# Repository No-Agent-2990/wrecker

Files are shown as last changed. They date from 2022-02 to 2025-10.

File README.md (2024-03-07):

# Wrecker
Mostly 3D printed design for linear drive machine. 3" of travel, compact and economical. 



(Safe) Video https://imgur.com/a/8FI21lm

Stainless Steel 1/4-20 rod is used though the load bearing assembly it is quite sturdy.

I apologize to all our metric friends for using imperial hardware, but it's cheap and easy to find here. I may do a version for M6 rod if there is some demand.

# Bill of Materials

## Filament
- PLA, PLA+, or PAL Pro

## Electronics:
- ESP32 Arduino - Hitlego PN ESP-WROOM-32 or eq
- 7x3cm proto PCB perfboard - from Elegoo CA-EL-CP-021 kit or eq
- 24VDC 4A power supply with barrel connector output - ALITOVE ALT-2404 or eq. An old 19.5V laptop supply should work too though a little slower.
- Barrel connector extension cord - must match 24VDC supply
- 24V to Micro USB 5V converter
- NEMA23 56mm Stepper, Bipolar, 2.8A, 2.5mH, 1.8deg - Steppers Online PN 23HS22-2804S or similar
- TB6600 Stepper motor driver
- (2) Hall Effect sensors AH3574-P-A
- 40mm Fan (24V or 5V) - 5V if powering from Arduino (recommended)
- (2) 10K linear potentiometers
- (2) 6" or longer servo extensions

## Hardware
- (1 or 2) 1/4-20 all-threaded Stainless Steel rod, 24" (304 or 18/8)
- 1/4-20 Hex coupler
- (6) 1/4-20 hex nuts
- (4) 1/4-20 washers
- (6) M4x25mm Cheese head
- (4) M4 rubber Grommets or (8) M4 rubber washers
- (4) M4 hex nuts
- (4) M4 lock washers
- (16) M3x8mm flat-head?
- (2) 1/4" dia,  1/16" thick disc magnets

## Other
- Attachment of your choice! End effector files compatible with vacuum-lock attachments and fleshlight are provided.

# Printing

- PLA is the recommended material. Its hard, smooth and abrasion resistant. It is not heat resistant!
- Print the STL files in the orientation provided.
- Files designed for printer line width of 0.5mm and later height of 0.25mm. This works well with 0.4mm nozzle
- 3 walls, 20% 3D infill like cubic

*No supports should be needed*

# Mechanical Assembly

## Preparation

## Stepper Driver setup
- Set current dip switch for 2.5A current limit
- Set dip switch for steps per pulse (micro-steps) to 32

### Base

Tap all the M3 holes in base for cover.
Tap M3 holes for TB6600 mounting.
Tap M3 hole for cable clamp
Press fit 1/4-20 nut into pocket, use 1/4 bolt from below to help seat if needed. If not secure, melt plastic around edge.
Tap the M4 holes for the handle.

### Cover

Attach plug to fan wires (if none), will need mate for attaching to proto board
Mount fan on inside and grill on outside using 4x M3x12mm flathead screws, lockwashers and nuts.
*Make sure airflow direction is _into_ case.*

### Slide

Remove and blobs and bumps with sharp knife. Clean out any crud in tube with 1/4" drill.
Put a drop of glue in the pockets, then push magnets into each pocket. Remove any excess glue.

### Pinion

Clean up gear teeth, shaft hole as needed.
Insert M2 hex nut into pocket in shaft, thread M2x4mm grub screw in nut, leave flush.

### Vacuum lock effector

Coat with a couple coats of spray-on acrylic to seal.

## Hall sensors

Cut servo extension leaving about 6 in" on the female end.
Attach wires to the 3 leads of female end, heat shrink. 
- Red: VDD pin
- Black: GND pin
- White: OUT pin

## Assembly

### Servo motor
*if using grommets*:
Place M4 grommets into base holes, and push M4x25mm throuh grommets from slide side to motor side

*if using rubber washers*:
Place M4x25mm through rubber washer, then through base, then add 2nd rubber washer.

Place motor over screw ends, with leads up. Add lock washer and nut to each screw, tighten.

### PCB
Mount 3x7 PCB with ESP32, wiring attached tp 4 mounting bosses with #2x1/4" self-tapping screws.

### 24V to USB converter

Mount to side of vertical fin with M3x8mm screws. Plug micro-usb end into ESP32.

### TB6600
Mount to base holes with M3x8mm cheese head screws.

Cut barrel extension cable near male end and discard male end and strip wire ends.
Twist + wire from barrel connector and + wire from 24V USB converter together and insert into (+) DC input

Twist - wire from barrel connector and - wire from 24V USB converter together and insert into (-) DC input
***OBSERVE POLARITY CAREFULLY***

See wiring section for details on connecting control signals to TB6600.

### Slide
Cut 8" piece of 1/4-20 rod, de-burr and reform threads with nut.
*(Note: If you don't care if the machine can be broken down for storage, you can just used a single 16~20" piece)*
Place through tube in slide. 
Add washer to end w/o the nut pocket.
Add nuts to both ends of the rod. Set nut on end with pocket flush with rod.
Tight nut on other end to draw nut into pocket. Torque firmly.

### Hall sensors
Slide hall sensors fully into troughs, angled face up.
Secure with dab of hot glue.

### Vacuum lock effector

Cut 12" length of 1/4-20 SS rod. Deburr rod ends, thread nut over to restore threads.
Place rod through tube. 
Thread hex not on tip end of rod until rod is flush with nut. 
Place washer on other end of rod, then nut. Tighten nut with whrench until top nut is pulled fully into pocket.

## Post-Assembly

Lubricate slide with silicone lubricant oil (not grease).
Lubricate pinion gear with silicone grease.

# Wiring

*add diagram here*

I recommned installing 0.1" center headers on the protoboard and connecting the control signals via jumpers or servo plugs.

The default ESP32 pins used are given in the arduino sketch ino file source code:
```
const int pulsePin = 23;          <- This is the stepper driver "step" pulse output pin
const int dirPin  = 22;           <- This is the stepper driver "direction" control output pin
const int enaPin = 21;            <- This is the stepper driver enable output pin
const int limitBackPin = 36;      <- This is the front hall sensor input pin
const int limitFwdPin = 39;       <- This is the rear hall sensor input pin
const int speedAdcPin = 34;       <- Speed potentionmeter analog input pin
const int strokeAdcPin = 35;      <- Length potentiometer analog input pin
```
Configure TB6600 control wiring for common ground by connection the "-" terminal of each input of the TB6600 to arduino ground. 
*Note that the TB6600 control input grounds and TB6600 power ground are all isolated from eachother inside the TB6600!* 

Connect the appropriate ("pulse", "dir", "ena") GPIO pin of the ESP32 to the appropriate (+) control inputs on the TB6600.

Arduino sketch will drive the pin high (3.3V) to activate.

Connect hall sensors to ESP32 3.3V power (red wire), gnd (black), and appropriate GPIO pins (white).
*Note that the EPS32 signals are 3.3V IO, and do not support 5V levels!*

# Arduino
Code provided is written for the ESP32 which has dual 240MHz cores, and can run the stepper at its highest rate easily. It also has Wifi functionality built in. Any Arduino or other controller could probably be used but will not work with the provided code.

I used this stepper lib:

https://github.com/gin66/FastAccelStepper

I used these tutorials to develop the wifi and webserver:

https://randomnerdtutorials.com/esp32-dual-core-arduino-ide/

https://randomnerdtutorials.com/esp32-servo-motor-web-server-arduino-ide/

The randomnerdtutorials.com site has good tuturial how to install the needed components in the IDE. It's a bit complicated.

## Build Setup

## Code

All the sketch code is in the main ino file.

The network.h file has wifi network setup.

## Configuration

# Operation

Attach rod segment with end effector to slide shaft rod using the hex coupler with a additional nut on each side. Tight the nuts to lock in place. A 3D printable finger wrench is included.

Plug in power, wait for Wifi to initialize and/or connect, and the linear drive to auto-home. 
Adjust speed/stroke with sliders as desired.

If no device is connected to the web server, the on-board control knobs remain active. Once a web client connects, they knobs are inactive. If the web client disconnects, the knobs become active again.
...

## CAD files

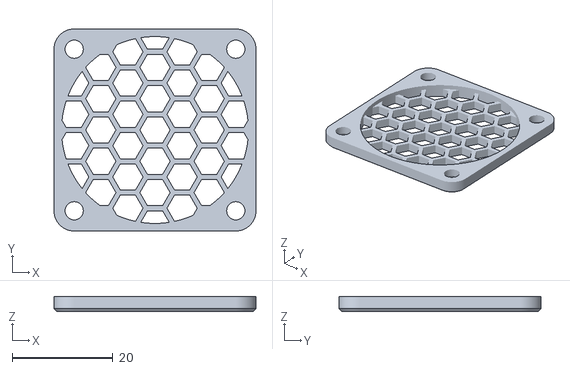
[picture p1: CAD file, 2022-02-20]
stl/fan-FanGrille.stl
40.0 x 40.0 x 3.00

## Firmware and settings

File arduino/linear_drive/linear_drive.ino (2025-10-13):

// linear_drive

#define WEB   // Enable Web control interface
#define STA   // Enable Wifi Station mode to connect to exisint network (else use AP mode)

#include <stdint.h>
// for AVR only #include <AVRStepperPins.h>
#include <Arduino.h>
#include <common.h>

#ifdef WEB
  // For web interface
  #include <WiFi.h>
  #include <AsyncTCP.h>
  #include <ESPAsyncWebServer.h>
  #include "SPIFFS.h"
  #include <Arduino_JSON.h>
#endif

#include <FastAccelStepper.h>
#include <PoorManFloat.h>
#include <RampCalculator.h>
#include <RampGenerator.h>
#include <StepperISR.h>

// Put network info here:
#include "./network.h"

// Defines
#define PITCH_DIAM_MM   30
#define STEPS_REV       200
#define USTEPS          32L        // number of micro-steps per step

const int ledPin = 2;   // Hitlego module
//const int ledPin = 16;  // Elegoo module
const int pulsePin = 23;
const int dirPin  = 22;
const int enaPin = 21;
const int limitBackPin = 36;
const int limitFwdPin = 39;
const int speedAdcPin = 34;
const int strokeAdcPin = 35;

int dirFwd = true;
int runState = false;
int usePots = true;
int useWeb = false;
long stepSpeed = 125 * USTEPS;
long stepSpeedMax = 4000 * USTEPS;
long stepAcc = 125 * USTEPS;
long stepAccMax = 40000 * USTEPS;   // this really depends on weight of payload
long stroke = 125 * USTEPS;
long strokeMax = 160 * USTEPS;
long strokeOffset = 0 * USTEPS;
long startTime, deltaTime;

FastAccelStepperEngine engine = FastAccelStepperEngine();
FastAccelStepper *stepper = NULL;

void homeStepper();
long setSpeedAcc(long newStepSpeed);


//////////////////////////////////////////////////////////////////////////////////////////////////
//////////////////////////////////////////////////////////////////////////////////////////////////
#ifdef WEB

  const char* sta_hostap_ssid = STA_HOSTAP_SSID;
  const char* sta_hostap_pwd = STA_HOSTAP_PWD;
  
  const char* ap_ssid = AP_SSID;
  const char* ap_pwd = AP_PWD;
  IPAddress Ip = AP_IPADDR;
  IPAddress NMask = AP_NETMASK;
  
  // Create AsyncWebServer object on port 80
  AsyncWebServer server(80);
  // Create a WebSocket object
  
  AsyncWebSocket ws("/ws");
  // Set LED GPIO
  const int ledPin1 = 12;
  const int ledPin2 = 13;
  const int ledPin3 = 14;
  
  String message = "";
  String sliderValue1 = "0";
  String sliderValue2 = "0";
  String sliderValue3 = "0";
  
  int dutyCycle1;
  int dutyCycle2;
  int dutyCycle3;
  
  // setting PWM properties
  const int freq = 5000;
  const int ledChannel1 = 0;
  const int ledChannel2 = 1;
  const int ledChannel3 = 2;
  
  const int resolution = 8;
  
  //Json Variable to Hold Slider Values
  JSONVar sliderValues;
  
  //Get Slider Values
  String getSliderValues(){
    sliderValues["sliderValue1"] = String(sliderValue1);
    sliderValues["sliderValue2"] = String(sliderValue2);
    sliderValues["sliderValue3"] = String(sliderValue3);
  
    String jsonString = JSON.stringify(sliderValues);
    return jsonString;
  }
  
  // Initialize SPIFFS
  void initFS() {
    if (!SPIFFS.begin()) {
      Serial.println("An error has occurred while mounting SPIFFS");
    }
    else{
     Serial.println("SPIFFS mounted successfully");
    }
  }
  
  // Initialize WiFi
 void initWiFi() {
    int i = 0;
#ifdef STA
    WiFi.mode(WIFI_STA);
    WiFi.begin(sta_hostap_ssid, sta_hostap_pwd);
    Serial.print("Connecting to WiFi ..");
    while ((i < 15) && (WiFi.status() != WL_CONNECTED)) {
      Serial.print('.');
      delay(1000);
      i++;
    }
    if (WiFi.status() == WL_CONNECTED) {
      Serial.print("Connected to AP ");
      Serial.println(sta_hostap_ssid);
      Serial.print("AP assigned IP ");
      Serial.println(WiFi.localIP());
    }
    else {
      Serial.print("STA mode could not connect to AP ");
      Serial.println(sta_hostap_ssid);
      Serial.println("Falling back to AP mode...");

      // fall back to AP mode
      WiFi.mode(WIFI_AP);
      WiFi.softAP(ap_ssid, ap_pwd);
      delay(100);
      WiFi.softAPConfig(Ip, Ip, NMask);
      delay(100);
      Serial.print("Started AP SSID ");
      Serial.println(ap_ssid);
      Serial.print("Static IP ");
      Serial.println(WiFi.softAPIP());      
    }
#else
    // WIFI AP
    WiFi.mode(WIFI_AP);
    WiFi.softAP(ap_ssid, ap_pwd);
    delay(100);
    WiFi.softAPConfig(Ip, Ip, NMask);
    delay(100);
    Serial.print("Started AP SSID ");
    Serial.println(ap_ssid);
    Serial.print("Static IP ");
    Serial.println(WiFi.softAPIP());
#endif    
  }
  
  void notifyClients(String sliderValues) {
    ws.textAll(sliderValues);
  }
  
  void handleWebSocketMessage(void *arg, uint8_t *data, size_t len) {
    AwsFrameInfo *info = (AwsFrameInfo*)arg;
    if (info->final && info->index == 0 && info->len == len && info->opcode == WS_TEXT) {
      data[len] = 0;
      message = (char*)data;
      if (message.indexOf("1s") >= 0) {
        sliderValue1 = message.substring(2);
        dutyCycle1 = map(sliderValue1.toInt(), 0, 100, 0, 255);
        Serial.println(dutyCycle1);
        Serial.print(getSliderValues());
        notifyClients(getSliderValues());
      }
      if (message.indexOf("2s") >= 0) {
        sliderValue2 = message.substring(2);
        dutyCycle2 = map(sliderValue2.toInt(), 0, 100, 0, 255);
        Serial.println(dutyCycle2);
        Serial.print(getSliderValues());
        notifyClients(getSliderValues());
      }    
      if (message.indexOf("3s") >= 0) {
        sliderValue3 = message.substring(2);
        dutyCycle3 = map(sliderValue3.toInt(), 0, 100, 0, 255);
        Serial.println(dutyCycle3);
        Serial.print(getSliderValues());
        notifyClients(getSliderValues());
      }
      if (strcmp((char*)data, "getValues") == 0) {
        notifyClients(getSliderValues());
      }
    }
  }
  void onEvent(AsyncWebSocket *server, AsyncWebSocketClient *client, AwsEventType type, void *arg, uint8_t *data, size_t len) {
    switch (type) {
      case WS_EVT_CONNECT:
        Serial.printf("WebSocket client #%u connected from %s\n", client->id(), client->remoteIP().toString().c_str());
        usePots = false;
        useWeb = true;
        break;
      case WS_EVT_DISCONNECT:
        Serial.printf("WebSocket client #%u disconnected\n", client->id());
        break;
      case WS_EVT_DATA:
        handleWebSocketMessage(arg, data, len);
        break;
      case WS_EVT_PONG:
      case WS_EVT_ERROR:
        break;
    }
  }
  
  void initWebSocket() {
    ws.onEvent(onEvent);
    server.addHandler(&ws);
  }

#endif  // ifdef WEB
//////////////////////////////////////////////////////////////////////////////////////////////////
//////////////////////////////////////////////////////////////////////////////////////////////////


void setup() {

  // Limit Switches
  pinMode(limitBackPin, INPUT_PULLUP);
  pinMode(limitFwdPin, INPUT_PULLUP);

  Serial.begin(115200);
  Serial.println("*** Hello from linear_drive! ***");
  Serial.println("");
  Serial.println("");
  Serial.println("");

#ifdef WEB
  initFS();
  initWiFi();
  initWebSocket();
  
  // Web Server Root URL
  server.on("/", HTTP_GET, [](AsyncWebServerRequest *request){
    request->send(SPIFFS, "/index.html", "text/html");
  });
  
  server.serveStatic("/", SPIFFS, "/");

  // Start server
  server.begin();
#endif

   engine.init();
   engine.setDebugLed(ledPin);
   stepper = engine.stepperConnectToPin(pulsePin);

   if (stepper) {
      stepper->setDirectionPin(dirPin, true);
      stepper->setEnablePin(enaPin, true);
      stepper->setAutoEnable(false);
      // If auto enable/disable needs, just add (one or both):
      stepper->setDelayToEnable(50);
      stepper->setDelayToDisable(1000);

      stepSpeed = 125 * USTEPS;
      stepper->setSpeedInHz(stepSpeed);       // steps/s
      stepper->setAcceleration(stepSpeed);  // steps/s²

      Serial.println("Stepper alignment starting...");
      homeStepper();
   } else {
      Serial.println("ERROR - Create stepper failed!");    
      while(true){};
   }

    engine.setDebugLed(ledPin);
    startTime = millis();
}

////////////////////////////////////////////////////////////////////////////////////
// put your main code here, to run repeatedly
////////////////////////////////////////////////////////////////////////////////////
void loop() {


    // Check Limit Switches
    if (!digitalRead(limitBackPin)) {
        stepper->forceStopAndNewPosition(-USTEPS * 10);  // stops stepper the fastest
        Serial.println("Backward Limit Switch Tripped!");
        delay(200);        
        stepper->move(10*USTEPS); // back off
        delay(200);         // give it time to release limit sw
        homeStepper();
        runState = false;
    }
    else if (!digitalRead(limitFwdPin)) {
        stepper->forceStopAndNewPosition(strokeMax + USTEPS * 10);  // stops stepper the fastest, call this new spot past the end
        Serial.println("Forward Limit Switch Tripped!");
        delay(200);
        stepper->move(-10*USTEPS); // back off
        delay(200);         // give it time to release limit sw
        homeStepper();
        runState = false;
    }
      
    if (runState && !stepper->isRunning()) {
      if (dirFwd)
        stepper->moveTo(stroke);
      else
        stepper->moveTo(strokeOffset);
      dirFwd = !dirFwd;
      deltaTime = millis() - startTime;
      startTime = millis();
//        Serial.println(deltaTime);
//        delay(1);
    }

    // Check control knobs if enabled
    if (usePots) {
      strokeOffset = 0;
      readSpeedPot();
      readStrokePot();        
    }

    // Check web interface if enabled
    if (useWeb) {
      stroke = strokeMax *  dutyCycle2 / 255L; 
      if (stroke < (3 * USTEPS)) stroke = 3 * USTEPS;
      
      strokeOffset = strokeMax *  dutyCycle3 / 255L;
      if (strokeOffset > (stroke - 3 * USTEPS))
        strokeOffset = stroke - 3 * USTEPS;
        
      if (dutyCycle1 > 1) {
        setSpeedAcc(dutyCycle1 * stepSpeedMax / 511L);
        runState = true;          
      }
      else {
        if (runState)
          homeStepper();
        runState = false;          
      }        
    }

    // Check for serial interface commands
    checkSerial();

#ifdef WEB
  ws.cleanupClients();
#endif    
}

/////////////////////////////////////////////////////////////////////
// Bring linear drive to resting "home" position
/////////////////////////////////////////////////////////////////////
void homeStepper() {

    // gracefull stop 1st
    stepper->stopMove();
    while (stepper->isRunning()) {};
    stepper->enableOutputs();
    stepper->setAcceleration(250 * USTEPS);      // steps/s/s
    stepper->setSpeedInHz(125 * USTEPS);       // steps/s
    stepper->move((-strokeMax - 20) * USTEPS);
 
    while (digitalRead(limitBackPin)) {
        if (!digitalRead(limitFwdPin)) {
          stepper->forceStopAndNewPosition(strokeMax + 20 * USTEPS);
          Serial.println("Forward limit switch tripped while reversing!");
          stepper->disableOutputs();
          while(true){};
        }      
    }
    // Tripped reverse stop 
    stepper->forceStopAndNewPosition(-10 * USTEPS);  // stops stepper the fastest
    delay(100);    

    // Move forward until switch clears
    stepper->move(50 * USTEPS);    
    while (!digitalRead(limitBackPin)) {
    }
    stepper->forceStopAndNewPosition(-2 * USTEPS);  // call this spot "-2"    
    delay(50);
    stepper->moveTo(0);
    Serial.println("Stepper home finished.");
}

/////////////////////////////////////////////////////////////////
// Sets travel movement speed limit and accelleration
// Accelleration is set to reach speed limit in 1/3 of stroke
// So movement will consist of 3 equal distance phases:
// 1. Linear accelleration to speed
// 2. Coast at speed
// 3. Deaccelleration to stop
/////////////////////////////////////////////////////////////////
long setSpeedAcc(long newStepSpeed) {

  long distance = stroke - strokeOffset;
  stepSpeed = newStepSpeed;
  
  if (stepSpeed < 100 * USTEPS)
    stepSpeed = 100 * USTEPS;
  
  if (stepSpeed > stepSpeedMax)
    stepSpeed = stepSpeedMax;
     
  // set accelleration based on kinematic eq Vf^2 = 2*a*d => a = v^2 /(2*d))
  // The value of "a" will reach full velocity at 1/3 of stroke is:
  //      a = v^2 /(2*d/3))
  // Scaled to avoid integer overflow in square => a = 128 * (v/16)^2 * (d/3)
  if (distance < 3) { // avoid divide by zero
    Serial.println("Distance too small to set acc");
    stepAcc = 1;
    return stepAcc;
  }
  stepAcc = 128L * (((stepSpeed/16)*(stepSpeed/16)) / (distance/3));
  if (stepAcc > stepAccMax)
    stepAcc = stepAccMax;
  else if (stepAcc < 125 * USTEPS)
    stepAcc = 125 * USTEPS;
  stepper->setAcceleration(stepAcc);      // steps/s/s
  stepper->setSpeedInHz(stepSpeed);       // steps/s
  
  // this messes up moves in progress and hits limit sw!!!!!!!!!!!!!!!!!!!!!!!!!!!!!!
  // stepper->applySpeedAcceleration();        // Apply don't wait for next move command
  
//  Serial.print("stepSpeed ");
//  Serial.println(stepSpeed);
//  Serial.print("stepAcc ");
//  Serial.println(stepAcc);
  
  return stepSpeed;
}

/////////////////////////////////////////////////////////////////
long readSpeedPot() {  

  static long speedPotReadingAvg = 0;
  static long speedPotReadingLast = 0;
  long speedPotReading;
  
  speedPotReading = analogRead(speedAdcPin);
  speedPotReadingAvg = (speedPotReading + 127UL * speedPotReadingAvg) / 128UL;
  if (std::abs(speedPotReadingAvg - speedPotReadingLast) > 15)
  {
//    Serial.print("speedPotReadingAvg ");
//    Serial.println(speedPotReadingAvg);
    speedPotReadingLast = speedPotReadingAvg;
  
    if (speedPotReadingAvg > 50) {
      setSpeedAcc(speedPotReadingAvg * USTEPS / 2);
      runState = true;          
    }
    else {
      if (runState)
        homeStepper();
      runState = false;          
    }        
  }
  return speedPotReadingAvg;
}

/////////////////////////////////////////////////////////////////
long readStrokePot() {  

  static long strokePotReadingAvg = 0;
  static long strokePotReadingLast = 0;
  long strokePotReading;
  
  strokePotReading = analogRead(strokeAdcPin);
  strokePotReadingAvg = (strokePotReading + 127UL * strokePotReadingAvg) / 128UL;
  if (std::abs(strokePotReadingAvg - strokePotReadingLast) > 1)
  {
//    Serial.print("strokePotReadingAvg ");
//    Serial.println(strokePotReadingAvg);
    strokePotReadingLast = strokePotReadingAvg;
    stroke = strokeMax * strokePotReadingAvg / 4096L; 
    if (stroke < (3 * USTEPS)) stroke = 3 * USTEPS;
    // If stroke is changed we need to recompute accelleration
    // Call with current speed will recalculate acc for new stroke
    setSpeedAcc(stepSpeed);

    Serial.print("stroke ");
    Serial.println(stroke);
  }

  // vibration mode
//  if (stroke <= (5 * USTEPS)) {
//    setSpeedAcc(stepSpeedMax);
//  }

  return strokePotReadingAvg;
}

/////////////////////////////////////////////////////////////////
int checkSerial() {
  if (Serial.available()) {
    char rxc[2];
    Serial.readBytes(rxc,1);
    
    switch(rxc[0]) {
      case '1':  stepSpeed = 125 * USTEPS;
            runState = true;
          break;
      case '2':  stepSpeed = 185 * USTEPS;
            runState = true;
          break;
      case '3':  stepSpeed = 280 * USTEPS;
            runState = true;
          break;
      case '4':  stepSpeed = 425 * USTEPS;
            runState = true;
          break;
      case '5':  stepSpeed = 635 * USTEPS;
            runState = true;
          break;
      case '6':  stepSpeed = 950 * USTEPS;
            runState = true;
          break;
      case '7':  stepSpeed = 1425 * USTEPS;
            runState = true;
          break;
      case '8':  stepSpeed = 2130 * USTEPS;
            runState = true;
          break;
      case '9':  stepSpeed = 3200 * USTEPS;
            runState = true;
          break;
      case '0':  stepSpeed = 125 * USTEPS;            
            stepper->moveTo(0);
            runState = false;
            dirFwd = true;
          break;
      case 'h':  stepSpeed = 125 * USTEPS;
            runState = false;
            dirFwd = true;
            homeStepper();
          break;
      case 's':  stroke = 100 * USTEPS;
          break;
      case 'm':  stroke = 125 * USTEPS;
          break;
      case 'l':  stroke = strokeMax;
          break;
      case 'v':  stroke = USTEPS;
          break;
      case 'x':  stroke = strokeMax + 500;   // designed to overextend
          break;
      case '+':  stepSpeed += 125 * USTEPS;
          break;
      case '-':  stepSpeed -= 125 * USTEPS;
          break;
      case '>':  stroke += USTEPS;
          break;
      case '<':  stroke -= USTEPS;
          break;
      case 'p':  usePots = !usePots;
            if (usePots) Serial.println("Pots enabled");
            else Serial.println("Pots disabled");
          break;
      default:  break;
    }
    if (stroke < USTEPS) stroke = USTEPS;
    else if (stroke > 200 * USTEPS) stroke = 200 * USTEPS;
    setSpeedAcc(stepSpeed);
    return true;
  } else {
    return false;    
  }
}

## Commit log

2022-02-20 add str, arduino code
2022-02-20 add fan grill, position stls for printing
    [fan-FanGrille.stl]
2024-03-07 add more description of the wiring of the TB6600 to the ESP32
